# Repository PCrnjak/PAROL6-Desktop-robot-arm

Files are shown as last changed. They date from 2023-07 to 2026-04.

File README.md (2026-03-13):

<div align="center">

# PAROL6-Desktop-robot-arm

</div>

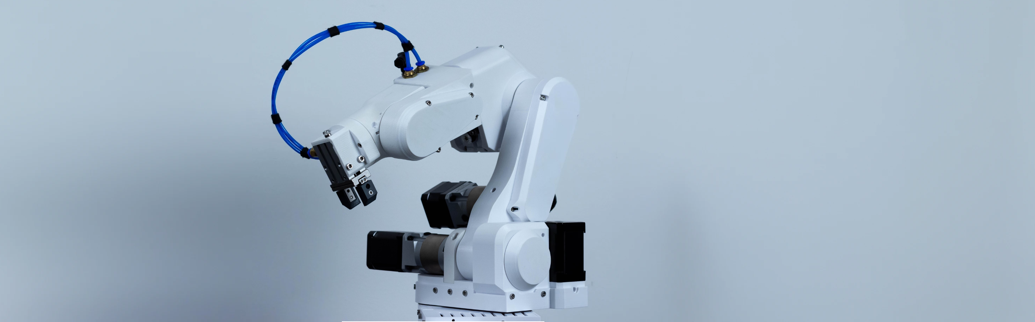
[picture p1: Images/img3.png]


<div align="center">

      Powered by the Robotics Toolbox (https://github.com/petercorke/robotics-toolbox-python) 

<p align="center">
  
  
  
  
  
  
</p>

## [▶️YouTube🔴 Video of Robot in Action!](https://youtu.be/bbrFn3aFLaA)

</div>

## 📖 Project Overview
PAROL6 is a high-performance 3D-printed desktop robotic arm. The design approach of PAROL6 was to be similar to industrial robots in terms of mechanical design, control software, and usability. Control software, GUI, and robots STL files are open-source. 

## How to build / Where to buy?

You can buy the PAROL6 robotic arm on our website: https://source-robotics.com

If you want to Source all the parts yourself and build your own follow these steps:

* Source all the parts from the [BOM](https://github.com/PCrnjak/PAROL6-Desktop-robot-arm/tree/main/BOM)
* Follow [Building instructions](https://github.com/PCrnjak/PAROL6-Desktop-robot-arm/tree/main/Building%20instructions) to assemble your robot
* Follow [DOCS](https://source-robotics.github.io/PAROL-docs/) to get your robot up and running.

## 📚 Resources
- [Official website](https://source-robotics.com)
- [Commander software](https://github.com/PCrnjak/PAROL-commander-software) ------ [Minimal hardware specs!](https://github.com/PCrnjak/PAROL-commander-software/blob/main/confirmed_working_systems.md)
- [Python API](https://github.com/PCrnjak/PAROL6-python-API) ; [Python API legacy](https://github.com/PCrnjak/PAROL6-python-API-Alvar)
- [Building instructions](https://github.com/PCrnjak/PAROL6-Desktop-robot-arm/tree/main/Building%20instructions)
- [BOM](https://github.com/PCrnjak/PAROL6-Desktop-robot-arm/tree/main/BOM)
- [DOCS](https://source-robotics.github.io/PAROL-docs/)
- [Video tutorials](https://youtube.com/playlist?list=PLSueoDrBt5MMTL9O8qAWZiJrNIf8-29Qz&si=Zca3UZKENje9ifow)
- [ROS2 / Moveit simulation](https://github.com/PCrnjak/PAROL6-ROS2-MOVEIT)

### Community projects
- [WEB commander software](https://github.com/Jepson2k/PAROL-Web-Commander)
- [Commander software refactored for easier editing + vision systems](https://github.com/thousands-star/Parol6_Better_Command)
- [PAROL6 Gemini LLM vision control](https://github.com/AlvarEhr/PAROL6-Python-API-Gemini-Vision-Public)
- [PAROL6 Pilot webgui](https://github.com/jointAxis77/pilot)
- [Another GUI](https://github.com/jakubgrzebien1234-creator/PAROL6_GUI)
- [Tic Tac Toe with vision](https://github.com/lennardkiebler-cryptoii/Tic-Tac-Toe-Robot-Project-Parol6/tree/main)
  
## 🌐 More about PAROL6 robotic arm

| YouTube | Instagram | Twitter | LinkedIn |
|---|---|---|---|
|  |  |  |  |

| Discord | Forum | Hackaday | Blog |
|---|---|---| ---|
|  |  |  |  

## ⚠️ Safety, Liability & Disclaimer
This project includes experimental software, hardware designs, and assembly documentation that are still under development and may contain bugs, errors, or incomplete features. By using, building, or modifying this project, you acknowledge that:

* You use this project entirely at your own risk
* You are solely responsible for safe assembly, testing, and operation
* No guarantee is made regarding correctness, safety, or reliability
* The authors are not responsible for any damage, injury, or loss resulting from the use or misuse of this project
* Hardware performance and safety depend on user assembly, component quality, calibration, and handling, which cannot be guaranteed
* This project is provided “as is.” If you choose to build a device yourself using these files, designs, or instructions, you do so without any warranties or guarantees, including regarding safety, reliability, or suitability for any particular purpose.

THIS PROJECT INVOLVES LETHAL VOLTAGES AND OTHER SERIOUS HAZARDS THAT CAN CAUSE SEVERE INJURY. YOU MUST READ THE FULL [SAFETY WARNING AND DISCLAIMER DOCUMENT](SAFETY_WARNING_AND_DISCLAIMER.md)  BEFORE USING ANY PROJECT FILES. BY PROCEEDING, YOU ACKNOWLEDGE AND ACCEPT ALL RISKS AND AGREE TO USE THIS PROJECT ENTIRELY AT YOUR OWN RESPONSIBILITY.

## 💸Support us

The majority of this project is open source and freely available to everyone. Your assistance, whether through donations or advice, is highly valued. Thank you!

 


## 🛡️ Licensing
Project is under GPLv3 Licence

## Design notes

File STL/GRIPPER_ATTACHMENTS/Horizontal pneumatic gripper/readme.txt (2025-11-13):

If anyone interested I made a horizontal mount for the pneumatic griper. 
2x m4 x 10 for the gripper
4x m4 x 10 for the flange 
1x m4 x 6 for mounting it on the shaft
1x m4 x 20mm for the sensor.

First screw the gripper into the mount into the sunk holes
Screw in half way the 6mm screw into the flange
Mount the flange
Screw in the 20mm long one on the side until the end, It should be flush or extruding a bit on the other side
Bottom down the flange on the motor shaft, and tighten the screw.

When the robot is off try to rotate J6 it should move freely.

Prepare the gripper on the actuator, so you are turning J6+ direction until the gripper is flat. That way when you turn off the robot and it homes again, it will home the same, and not 360 rotated around.

The 2 files are the same STLs, but the "custom" was the first one, and i decided to rebuild the robot with self tapping inserts. The flange mounting holes are prepared for those inserts.

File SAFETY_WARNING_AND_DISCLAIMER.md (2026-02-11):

# Safety Warning & Disclaimer
## Definitions

For the purposes of this Safety Warning & Disclaimer, “PROJECT” refers to all materials, files, designs, models, simulations, URDF/MJCF files, control software, firmware, documentation, and any modifications or derivatives provided as part of this robotic arm project.

# Safety Warning

THIS PROJECT INVOLVES ROBOTIC SYSTEMS WITH MOVING MECHANICAL PARTS, ACTUATORS, MOTORS, ELECTRICAL POWER SYSTEMS, AND SOFTWARE-CONTROLLED MOTION. IMPROPER DESIGN, ASSEMBLY, CONFIGURATION, OR OPERATION CAN RESULT IN UNEXPECTED MOVEMENT, PINCH POINTS, CRUSH HAZARDS, COLLISIONS, ELECTRICAL SHOCK, PROPERTY DAMAGE, SERIOUS INJURY, OR DEATH.

Robotic arms can generate significant forces and move at high speeds. Even small systems may cause injury if safety precautions are not followed. Simulation results may not accurately represent real-world behavior, and transferring control software from simulation to physical hardware introduces additional risks.

ONLY QUALIFIED INDIVIDUALS WITH APPROPRIATE TRAINING AND EXPERIENCE IN ROBOTICS, MECHANICAL SYSTEMS, AND ELECTRICAL SYSTEMS SHOULD BUILD, MODIFY, OR OPERATE ANY PHYSICAL IMPLEMENTATION OF THIS PROJECT. ALWAYS FOLLOW APPLICABLE SAFETY STANDARDS, LOCAL REGULATIONS, AND BEST PRACTICES FOR ROBOTIC SYSTEMS. USE APPROPRIATE SAFETY MEASURES INCLUDING, BUT NOT LIMITED TO, EMERGENCY STOPS, PHYSICAL GUARDS, SOFTWARE LIMITS, AND PERSONAL PROTECTIVE EQUIPMENT.

IF YOU DO NOT FULLY UNDERSTAND THE RISKS ASSOCIATED WITH ROBOTIC SYSTEMS, DO NOT USE, BUILD, OR DEPLOY THIS PROJECT ON PHYSICAL HARDWARE.

# Disclaimer

THE PROJECT IS PROVIDED “AS IS”, WITHOUT WARRANTY OF ANY KIND, EXPRESS OR IMPLIED, INCLUDING BUT NOT LIMITED TO THE WARRANTIES OF MERCHANTABILITY, FITNESS FOR A PARTICULAR PURPOSE, OR NON-INFRINGEMENT.

BY USING THIS PROJECT, YOU ACKNOWLEDGE AND ACCEPT ALL RISKS ASSOCIATED WITH ITS USE, INCLUDING RISKS ARISING FROM SOFTWARE ERRORS, SIMULATION INACCURACIES, CONTROL FAILURES, HARDWARE MALFUNCTIONS, OR IMPROPER CONFIGURATION.

IN NO EVENT SHALL THE AUTHORS, CONTRIBUTORS, OR COPYRIGHT HOLDERS BE LIABLE FOR ANY CLAIM, DAMAGE, INJURY, DEATH, OR OTHER LIABILITY, WHETHER IN AN ACTION OF CONTRACT, TORT, OR OTHERWISE, ARISING FROM, OUT OF, OR IN CONNECTION WITH THE PROJECT OR THE USE OR OTHER DEALINGS IN THE PROJECT.

ANY ASSEMBLY, MODIFICATION, DEPLOYMENT, OR OPERATION OF THIS PROJECT — WHETHER IN SIMULATION OR ON PHYSICAL HARDWARE — IS PERFORMED ENTIRELY AT YOUR OWN RISK.

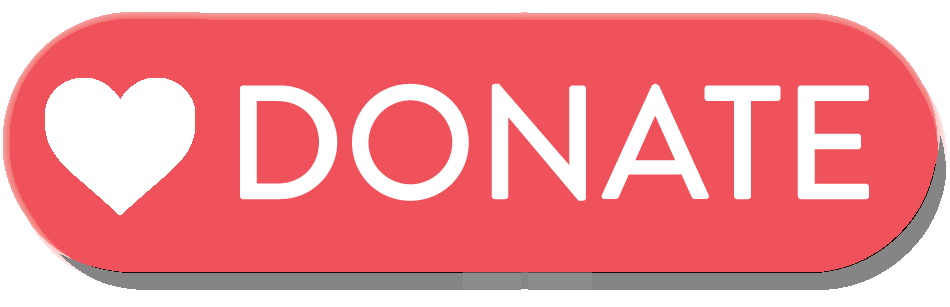
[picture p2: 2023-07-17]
Images/Donate.png

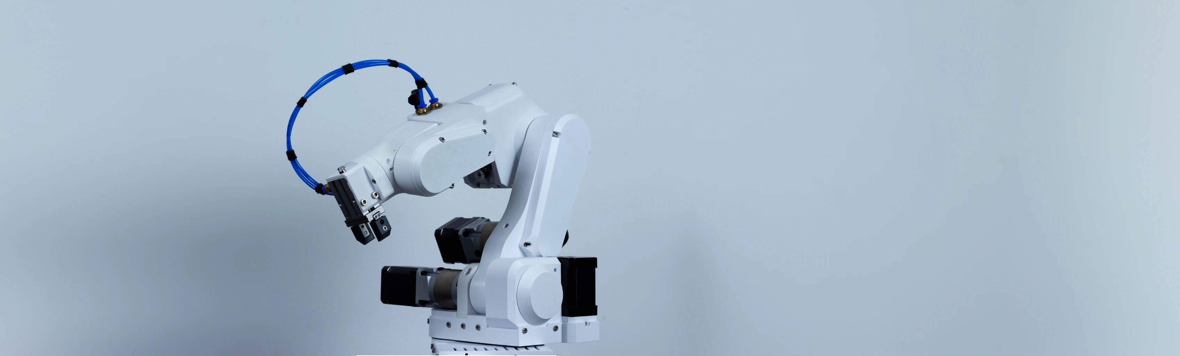
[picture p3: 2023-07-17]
Images/img2 - Copy.png

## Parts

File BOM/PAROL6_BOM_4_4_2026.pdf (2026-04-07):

### This file contains all the parts you need to build PAROL6 robot!

Most items have links where you can buy the item, and some of them are affiliate links. Items like screws, belts and bearings can be bought locally or from many other vendors.

Screws and nuts:
diameter , length | quantity | Description | Link M4x10mm | 20 | DIN 912 / ISO 4762 (hexagon socket head cap) M3x8mm | 10 | 2 mm head height M3x8mm | 50 | DIN 912 / ISO 4762 (hexagon socket head cap) M3x14mm | 30 | DIN 912 / ISO 4762 (hexagon socket head cap) M3 nut | 10 | DIN 912 / ISO 4762 (hexagon socket head cap) M3x25mm | 10 | DIN 912 / ISO 4762 (hexagon socket head cap) M2x10mm | 10 | DIN 912 / ISO 4762 (hexagon socket head cap) M3x16mm | 10 | DIN 912 / ISO 4762 (hexagon socket head cap) M3x6mm | 10 | Pan head phillips M3x12mm | 30 | DIN 912 / ISO 4762 (hexagon socket head cap) M3x35mm | 10 | DIN 912 / ISO 4762 (hexagon socket head cap) M4x16mm | 30 | DIN 912 / ISO 4762 (hexagon socket head cap) M4x14mm | 10 | DIN 912 / ISO 4762 (hexagon socket head cap) M4x50mm | 10 | DIN 912 / ISO 4762 (hexagon socket head cap) M3x15mm | 2 | Tapered screw head Gearboxes: Name in building instructions | Type | quantity | Description | Link
For cheaper gearbox options you can use MG series planetary gearboxes. They have bigger backlash but are cheaper. | Link (https://www.omc-stepperonline.com/mg-series-planetary-gearbox) | Aliexpress Link (https://s.click.aliexpress.com/e/_oBYBoUP) Gearbox 20:1 | Nema 17 20:1 EG precision planetary | 2 | Link | Aliexpress Link Gearbox 10:1 | Nema 17 10:1 EG precision planetary | 1 | Link | Aliexpress Link Motors: Name in building instructions | Type | quantity | Description | Link
Stepper 1 | Nema 17 16Ncm,42x42x20mm | 1 | Link (https://www.omc-stepperonline.com/nema-17-bipolar-1-8deg-16ncm-22-6oz-in-1a-3-7v-42x42x20mm-4-wires-17hs08-1004s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) | Aliexpress Link (https://s.click.aliexpress.com/e/_oo1LTs7)
Stepper 2 | Nema 17 45Ncm,42x42x40mm | 3 | Link (https://www.omc-stepperonline.com/nema-17-bipolar-45ncm-64oz-in-2a-42x42x40mm-4-wires-w-1m-cable-connector-17hs16-2004s1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) | Aliexpress Link (https://s.click.aliexpress.com/e/_oC1Ii0v)
Stepper 3 | Nema 17 65Ncm,42x42x60mm | 2 | Link (https://www.omc-stepperonline.com/nema-17-bipolar-1-8deg-65ncm-92oz-in-2-1a-3-36v-42x42x60mm-4-wires-17hs24-2104s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) | Aliexpress Link (https://s.click.aliexpress.com/e/_opq2ugp) Belts: Name in building instructions | Type | quantity | Description | Link
Joint 1 belt | HTD3 396 | 1 | 6 mm width | Link (https://s.click.aliexpress.com/e/_Dn5FasX)
Joint 3 belt | HTD3 342 | 1 | 6 mm width | Link (https://s.click.aliexpress.com/e/_DeIf41z)
Joint 4 belt | HTD3 201 | 1 | 6 mm width | Link (https://s.click.aliexpress.com/e/_Dc9GUKX)
Joint 5 belt | HTD3 246 | 1 | 6 mm width | Link (https://s.click.aliexpress.com/e/_Dm2tHRd)
| Pulleys: Name in building instructions Type | quantity | Description | Link
J4 pulley, J5 pulley | HTD3M 12 tooth 5mm bore 10mm width | 2 | | Link (https://s.click.aliexpress.com/e/_DFYERWX)
J1 pulley | HTD3M 15 tooth 5mm bore 10mm width | 1 | Link (https://s.click.aliexpress.com/e/_DBVgkVp) Mechanical stuff: Name in building instructions | Type | quantity | Description | Link
Shaft coupler | Shaft coupler | 3 | 8 mm hole shaft, M4 screw holes | Link (https://s.click.aliexpress.com/e/_c2xnQgI7) Bearings: Name in building instructions | Type | quantity | Description | Link
Bearing 1 | AXK3552 | 1 | 35X52X4, needs to have top and bottom plate | Link (https://s.click.aliexpress.com/e/_Dk4bHg7)
Bearing 2 | NSK HR32906J | 5 | Joint 5, 4 and 3 | Link (https://s.click.aliexpress.com/e/_DcJMtBl)
Bearing 3 | NSK HR32907J | 4 | Joint 1 and 2 | Link (https://s.click.aliexpress.com/e/_DcJMtBl)
Tension bearing | Ball bearing 3x8x4 | 20 | Used for belt tension | Link (https://s.click.aliexpress.com/e/_DCjfgFV)
Tension bearing | Ball bearing 3x10x4 | 20 | Used for belt tension | Link (https://s.click.aliexpress.com/e/_DlA33Af)
| Electronics: Name in building instructions Type | quantity | Description | Link
| PAROL control board | 1 | source-robotics.com | Link (https://source-robotics.com/products/parol6-control-board)
| TMC5160 | 6 | Drivers from the links are tested. Use any other at own risk: (https://s.click.aliexpress.com/e/_c3DGg2hx) Link1 | Link2
| Thermal paste | 2 1 | Needed only if your control board has no drivers! 12mm 3-6V | Link (https://s.click.aliexpress.com/e/_oExnMEF) On/Off button Link
| JST PH 2.0mm 200mm 4PIN | 1 1 | For power button | Link (https://s.click.aliexpress.com/e/_DeObQ1D) Noctua NF-A4x20 5V 40mm
| Power connector - male + female | 1 1 | GX16 2PIN M8 sensor Female 4 pin | Link (https://s.click.aliexpress.com/e/_DcHjMfN) Gripper connector (electric) Link
| Power supply | 1 | Any 24V 5A supply (https://s.click.aliexpress.com/e/_olFOM5Z) | Link (https://www.omc-stepperonline.com/edr-120-24-mean-well-120w-24vdc-5a-115-230vac-din-rail-power-supply-edr-120-24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)
| Limit switches | 3 | Type ZW12-3 | Link (https://s.click.aliexpress.com/e/_DBq6eeF)
| Inductive sensor 1 | 1 | 4mm NPN NO - alternative link (https://s.click.aliexpress.com/e/_c3CMbO1h) | Link (https://s.click.aliexpress.com/e/_c40MRkk5)
| Inductive sensor 2 | 1 | GX-F8A | Link (https://s.click.aliexpress.com/e/_c4KR8GBT)
| Inductive sensor 3 | 1 | M5, NPN NO - alternative link (https://s.click.aliexpress.com/e/_c3CMbO1h) | Link (https://s.click.aliexpress.com/e/_c3zGvxrP)
Estop | 1 | Any NC estop | Link (https://s.click.aliexpress.com/e/_DD0VVnd) Cable gland for estop | 1 | PG7 type | Link M3 brass insert | 4 | M3, 6mm lenght | Link
Pneumatic connector - robot | 4 | 4 mm type PM | Link (https://www.aliexpress.com/item/4001338085412.html)
Pneumatic Gripper | 1 | MHZ2-16D | Link (https://s.click.aliexpress.com/e/_DD83OLZ)
Pneumatic gripper connector | 2 | PC4 - M5 | Link (https://s.click.aliexpress.com/e/_DkCJqUL)
Pneumatic tube | 5 meters | 1 meter, 4x2.5mm | Link (https://s.click.aliexpress.com/e/_DEhvFyJ)
xt30 connector female | 1 | used to deliver power to PAROL6 PCB | Link (https://s.click.aliexpress.com/e/_DllR7eL)
Stlink | 1 1 | Use link! Pin order needs to be: SWCLK,SWDIO,GND,3V3,5V Comms to the PC | Link (https://s.click.aliexpress.com/e/_DCPwBnn) USB B cable
5/2 solenoid air valve | 1 | 4mm tube connectors, 5/2, 24V | Link (https://s.click.aliexpress.com/e/_DDrw0Ux)
Vacuum gripper Name in building instructions Type | quantity | Description | Link
Suction cup gripper | 1 | | Link (https://www.aliexpress.com/item/4000538850003.html)
Vacuum generator | 1 | | Link (https://s.click.aliexpress.com/e/_DdTAyOZ)
4mm to 6mm coupler | 1 | | Link (https://s.click.aliexpress.com/e/_DeEEqHR)

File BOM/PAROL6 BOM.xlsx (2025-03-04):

This file contains all the parts you need to build PAROL6 robot!
Most items have links where you can buy the item, and some of them are affiliate links.
Items like screws, belts and bearings can be bought locally or from many other vendors.
 | Screws and nuts:
 | diameter , length | quantity | Description | Link | Alternative links
 | M4x10mm | 20 | DIN 912 / ISO 4762 (hexagon socket head cap)
 | M3x8mm | 10 | 2 mm head height
 | M3x8mm | 50 | DIN 912 / ISO 4762 (hexagon socket head cap)
 | M3x14mm | 30 | DIN 912 / ISO 4762 (hexagon socket head cap)
 | M3 nut | 10 | DIN 912 / ISO 4762 (hexagon socket head cap)
 | M3x25mm | 10 | DIN 912 / ISO 4762 (hexagon socket head cap)
 | M2x10mm | 10 | DIN 912 / ISO 4762 (hexagon socket head cap)
 | M3x16mm | 10 | DIN 912 / ISO 4762 (hexagon socket head cap)
 | M3x6mm | 10 | Pan head phillips
 | M3x12mm | 30 | DIN 912 / ISO 4762 (hexagon socket head cap)
 | M3x35mm | 10 | DIN 912 / ISO 4762 (hexagon socket head cap)
 | M4x16mm | 30 | DIN 912 / ISO 4762 (hexagon socket head cap)
 | M4x14mm | 10 | DIN 912 / ISO 4762 (hexagon socket head cap)
 | M4x50mm | 10 | DIN 912 / ISO 4762 (hexagon socket head cap)
 | M3x15mm | 2 | Tapered screw head
 | Gearboxes:
Name in building instructions | Type | quantity | Description | Link | Alternative (Note these gearboxes have bigger backslash and in turn your robot will be less precise if you use them)
Gearbox 20:1 | Nema 17 20:1 EG precision planetary | 2 | Link (https://www.omc-stepperonline.com/eg-series-planetary-gearbox-gear-ratio-20-1-backlash-20-arc-min-for-nema-17-stepper-motor-eg17-g20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) | Link (https://www.omc-stepperonline.com/eg-series-planetary-gearbox-gear-ratio-20-1-backlash-20-arc-min-for-nema-17-stepper-motor-eg17-g20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) | Link (https://www.omc-stepperonline.com/mg-series-planetary-gearbox-gear-ratio-20-1-backlash-30-arc-min-for-nema-17-stepper-motor-mg17-g20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)
Gearbox 10:1 | Nema 17 10:1 EG precision planetary | 1 | Link (https://www.omc-stepperonline.com/eg-series-planetary-gearbox-gear-ratio-10-1-backlash-15-arc-min-for-nema-17-stepper-motor-eg17-g10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) | Link (https://www.omc-stepperonline.com/eg-series-planetary-gearbox-gear-ratio-10-1-backlash-15-arc-min-for-nema-17-stepper-motor-eg17-g10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) | Link (https://www.omc-stepperonline.com/mg-series-planetary-gearbox-gear-ratio-10-1-backlash-30-arc-min-for-nema-17-stepper-motor-mg17-g10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)
 | Motors:
Name in building instructions | Type | quantity | Description | Link
Stepper 1 | Nema 17 16Ncm,42x42x20mm | 1 | Link (https://www.omc-stepperonline.com/nema-17-bipolar-1-8deg-16ncm-22-6oz-in-1a-3-7v-42x42x20mm-4-wires-17hs08-1004s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) | Link (https://www.omc-stepperonline.com/nema-17-bipolar-1-8deg-16ncm-22-6oz-in-1a-3-7v-42x42x20mm-4-wires-17hs08-1004s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)
Stepper 2 | Nema 17 45Ncm,42x42x40mm | 3 | Link (https://www.omc-stepperonline.com/nema-17-bipolar-45ncm-64oz-in-2a-42x42x40mm-4-wires-w-1m-cable-connector-17hs16-2004s1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) | Link (https://www.omc-stepperonline.com/nema-17-bipolar-45ncm-64oz-in-2a-42x42x40mm-4-wires-w-1m-cable-connector-17hs16-2004s1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)
Stepper 3 | Nema 17 65Ncm,42x42x60mm | 2 | Link (https://www.omc-stepperonline.com/nema-17-bipolar-1-8deg-65ncm-92oz-in-2-1a-3-36v-42x42x60mm-4-wires-17hs24-2104s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) | Link (https://www.omc-stepperonline.com/nema-17-bipolar-1-8deg-65ncm-92oz-in-2-1a-3-36v-42x42x60mm-4-wires-17hs24-2104s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)
 | Belts:
Name in building instructions | Type | quantity | Description | Link
Joint 1 belt | HTD3 396 | 1 | 6 mm width | Link (https://s.click.aliexpress.com/e/_Dn5FasX)
Joint 3 belt | HTD3 342 | 1 | 6 mm width | Link (https://s.click.aliexpress.com/e/_DeIf41z)
Joint 4 belt | HTD3 201 | 1 | 6 mm width | Link (https://s.click.aliexpress.com/e/_opwpKMM)
Joint 5 belt | HTD3 246 | 1 | 6 mm width | Link (https://s.click.aliexpress.com/e/_ompnL9w)
 | Pulleys:
Name in building instructions | Type | quantity | Description | Link
J4 pulley, J5 pulley | HTD3M 12 tooth 5mm bore 10mm width | 2 |  | Link (https://s.click.aliexpress.com/e/_DFYERWX)
J1 pulley | HTD3M 15 tooth 5mm bore 10mm width | 1 |  | Link (https://s.click.aliexpress.com/e/_DBVgkVp)
 | Mechanical stuff:
Name in building instructions | Type | quantity | Description | Link
Shaft coupler | Shaft coupler | 3 | 8 mm hole shaft, M4 screw holes | Link (https://s.click.aliexpress.com/e/_DdSVv79)
 | Bearings:
Name in building instructions | Type | quantity | Description | Link
Bearing 1 | AXK3552 | 1 | 35X52X4, needs to have top and bottom plate | Link (https://s.click.aliexpress.com/e/_Dk4bHg7)
Bearing 2 | NSK HR32906J | 5 | Joint 5, 4 and 3 | Link (https://s.click.aliexpress.com/e/_oEMEtzK)
Bearing 3 | NSK HR32907J | 4 | Joint 1 and 2 | Link (https://s.click.aliexpress.com/e/_DcJMtBl)
Tension bearing | Ball bearing 3x8x4 | 20 | Used for belt tension | Link (https://s.click.aliexpress.com/e/_DCjfgFV)
Tension bearing | Ball bearing 3x10x4 | 20 | Used for belt tension | Link (https://s.click.aliexpress.com/e/_DlA33Af)
 | Electronics:
Name in building instructions | Type | quantity | Description | Link
 | PAROL control board | 1 | source-robotics.com | Link (https://source-robotics.com/products/parol6-control-board)
 | TMC5160 | 6 | Drivers from the links are tested. Use any other at own risk: Link1 (https://s.click.aliexpress.com/e/_opQvIZd) | Link2 (https://s.click.aliexpress.com/e/_Dd8Cjkb)
 | Thermal CEMENT | 2 | Needed only if your control board has no drivers! | Link (https://s.click.aliexpress.com/e/_opNwYbw)
 | On/Off button | 1 | 12mm 3-6V | Link (https://s.click.aliexpress.com/e/_DBpZV3h)
 | JST PH 2.0mm 200mm 4PIN | 1 | For power button | Link (https://s.click.aliexpress.com/e/_DeObQ1D)
 | Noctua NF-A4x20 5V 40mm | 1
 | Power connector - male + female | 1 | GX16 2PIN | Link (https://s.click.aliexpress.com/e/_DcHjMfN)
 | Gripper connector (electric) | 1 | M8 sensor Female 4 pin | Link (https://s.click.aliexpress.com/e/_DDQz9iP)
 | Power supply | 1 | Any 24V 5A supply | Link (https://www.omc-stepperonline.com/edr-120-24-mean-well-120w-24vdc-5a-115-230vac-din-rail-power-supply-edr-120-24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)
 | Limit switches | 3 | Type ZW12-3 | Link (https://s.click.aliexpress.com/e/_DBq6eeF)
 | Inductive sensor 1 | 1 | 4mm NPN NO | Link (https://s.click.aliexpress.com/e/_Dk60HT9)
 | Inductive sensor 2 | 1 | GX-F8A | Link (https://s.click.aliexpress.com/e/_DEOqTIT)
 | Inductive sensor 3 | 1 | M5, NPN NO | Link (https://s.click.aliexpress.com/e/_DDhHytl)
 | Estop 19mm | 1 | Any NC estop | Link (https://s.click.aliexpress.com/e/_okbRavW)
 | Cable gland for estop | 1 | PG7 type | Link (https://s.click.aliexpress.com/e/_DdJj62p)
 | M3 brass insert | 4 | M3, 6mm lenght | Link (https://s.click.aliexpress.com/e/_DmZR9AN)
 | Pneumatic connector - robot | 4 | 4 mm type PM | Link (https://www.aliexpress.com/item/4001338085412.html)
 | Pneumatic Gripper | 1 | MHZ2-16D | Link (https://s.click.aliexpress.com/e/_DD83OLZ)
 | Pneumatic gripper connector | 2 | PC4 - M5 | Link (https://s.click.aliexpress.com/e/_DkCJqUL)
 | Pneumatic tube | 5 meters | 1 meter, 4x2.5mm | Link (https://s.click.aliexpress.com/e/_DEhvFyJ)
 | xt30 connector female | 1 | used to deliver power to PAROL6 PCB | Link (https://s.click.aliexpress.com/e/_DllR7eL)
 | Stlink | 1 | Use link! Pin order needs to be: SWCLK,SWDIO,GND,3V3,5V | Link (https://s.click.aliexpress.com/e/_DCPwBnn)
 | USB B cable | 1 | Comms to the PC
 | 5/2 solenoid air valve | 1 | 4mm tube connectors, 5/2, 24V | Link (https://s.click.aliexpress.com/e/_DDrw0Ux)
 | Vacuum gripper
Name in building instructions | Type | quantity | Description | Link
 | Suction cup gripper | 1 |  | Link (https://www.aliexpress.com/item/4000538850003.html)
 | Vacuum generator | 1 |  | Link (https://s.click.aliexpress.com/e/_DdTAyOZ)
 | 4mm to 6mm coupler | 1 |  | Link (https://s.click.aliexpress.com/e/_DeEEqHR)

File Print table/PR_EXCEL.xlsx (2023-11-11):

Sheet: 3D printed parts stats
THIS TABLE HAS SUGGESTIONS ON WHAT SETTINGS TO USE!
IT IS NOT CRITICAL TO FOLLOW IT BUT NOTE THAT THESE SETTINGS HAVE BEEN TESTED ON MUTLIPLE ROBOTS!
Part name | Position in arm | Supports | mass (g) | Infill type | Infill % | Time | Cooling % | Layer h | Top layers | Bot layers | Perimeters
Wrist | J6 | Minimal | 77.65 | honey | 40 | 7h51m | 15 | 0.2 LA | 6 | 4 | 3
Pneumatic gripper holder | J6 | None | 31 | honey | 40 | 2h52m | 15 | 0.2 LA | 6 | 4 | 3
J5 pulley | J5 | None | 20 | honey | 40 | 2h | 15 | 0.2 LA | 6 | 4 | 3
J5 part | J5 | Minimal | 114 | honey | 30 | 10h | 15 | 0.2 LA | 6 | 4 | 3
J5 belt lid | J5 | None | 20 | honey | 15 |  | 15 | 0.2 LA | 6 | 4 | 3
J5 electronics lid | J5 | None | 20 | honey | 15 |  | 15 | 0.2 LA | 6 | 4 | 3
Elbow part | J4 | alot | 215 | honey | 25 | 16h | 15 | 0.2 LA | 6 | 4 | 3
J4 limiter | J4 | None | 1 | honey | 80 | 2m | 15 | 0.2 LA | 6 | 4 | 3
J4 bearing backplate | J4 | None |  | honey |  |  | 15 | 0.2 LA | 6 | 4 | 3
 | J4 | None |  | honey |  |  | 15 | 0.2 LA | 6 | 4 | 3
Elbow lid 1 | J4 | None | 20 | honey | 20 | 1h46m | 15 | 0.2 LA | 6 | 4 | 3
Elbow lid 2 | J4 | None | 4 | honey | 20 | 15m | 15 | 0.2 LA | 6 | 4 | 3
Upper arm | J3 | Minimal | 220 | honey | 35 | 18h | 15 | 0.2 LA | 6 | 4 | 3
J3 limit switch lid | J3 | None | 4 | honey | 50 | 21m | 15 | 0.2 LA | 6 | 4 | 3
J3 pulley | J3 | None | 25 | honey | 50 | 2h42m | 15 | 0.2 LA | 6 | 4 | 3
J3 pulley input | J3 | None | 14 | honey | 50 | 1h16m | 15 | 0.2 LA | 6 | 4 | 3
Upper arm cover | J3 | minimal | 34 | honey | 15 | 2h | 15 | 0.2 LA | 6 | 4 | 3
J2_cover | J2 | None | 10 | honey | 20 | 42m | 15 | 0.2 LA | 6 | 4 | 3
J2_bering backplate | J2 | None | 10 | honey | 20 | 42m | 15 | 0.2 LA | 6 | 4 | 3
J1_belt_cover | J2 | None | 37 | honey | 20 | 2h | 15 | 0.2 LA | 6 | 4 | 3
J2_stepper_blocker | J2 | None | 7 | honey | 20 | 15m | 15 | 0.2 LA | 6 | 4 | 3
J1_turret_motor_holder | J2 | Minimal | 53 | honey | 80 | 6h | 15 | 0.2 LA | 6 | 4 | 3
J1_turret | J1 | Minimal | 210 | honey | 25 | 18h | 15 | 0.2 LA | 6 | 4 | 3
J1_lid_motor | J1 | Minimal | 9 | honey | 25 | 51m | 15 | 0.2 LA | 6 | 4 | 3
J1_rotation_shaft | J1 | none | 31 | honey | 50 | 3h34m | 15 | 0.2 LA | 6 | 4 | 3
J2_shaft | J2 | none | 43 | honey | 50 | 4h41m | 15 | 0.2 LA | 6 | 4 | 3
Electronics_cover | J1 | Minimal | 80 | honey | 20 | 6h | 15 | 0.2 LA | 6 | 4 | 3
J2 limit switch cover | J2 | Minimal | 3 | honey | 25 | 13m | 15 | 0.2 LA | 6 | 4 | 3
Electronics_case | J1 | Minimal |  | honey | 50 |  | 15 | 0.2 LA | 6 | 4 | 3
Fan_cover | J1 | Minimal |  | honey | 20 |  | 15 | 0.2 LA | 6 | 4 | 3
J1_bottom_lid | J1 | Minimal |  | honey | 25 |  | 15 | 0.2 LA | 6 | 4 | 3
Main_base | J1 | Minimal |  | honey | 50 |  | 15 | 0.2 LA | 6 | 4 | 3
HTD_48_J5_PULLEY | J5 | Minimal |  | honey | 60 |  | 15 | 0.2 LA | 6 | 4 | 3
J4_output_pulley | J1 | Minimal |  | honey | 50 |  | 15 | 0.2 LA | 6 | 4 | 3
Pneumatic_gripper_holder | Gripper | Minimal |  | honey | 30 |  | 15 | 0.2 LA | 6 | 4 | 3
J1_backplate | J1 | Minimal |  | honey | 50 |  | 15 | 0.2 LA | 6 | 4 | 3
J1_turret | J1 | Minimal |  | honey | 45 |  | 15 | 0.2 LA | 6 | 4 | 3
J2_limit_switch_cover |  | Minimal |  | honey | 50 |  | 15 | 0.2 LA | 6 | 4 | 3
J1_stepper_block | J1 | Minimal |  | honey | 45 |  | 15 | 0.2 LA | 6 | 4 | 3
Upper_arm_wires_cover | J3 | Minimal |  | honey | 45 |  | 15 | 0.2 LA | 6 | 4 | 3
38_pulley_J3 | J3 | Minimal |  | honey | 70 |  | 15 | 0.2 LA | 6 | 4 | 3
42_pulley | J3 | Minimal |  | honey | 70 |  | 15 | 0.2 LA | 6 | 4 | 3

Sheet: Wire_markings
4pin | Joint
 | 5
 | 4
 | 6
 | 2
 | 3
No color | 1
3pin | Joint
 | 4
 | 6
2pin | Joint

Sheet: BOM for prototype
Screws and nuts: |  |  | Gearboxes: |  | Bearings:
diameter , length | Type | quantity | Type | quantity | Type | quantity
 |  |  | Motors:
 |  |  | Type | quantity
 |  |  |  |  | Mechanical stuff
 |  |  | Belts |  | type | quantity
 |  |  | Type | quantity
 |  |  | Pulleys:
 |  |  | Type | quantity | Electronics
 |  |  |  |  | type | quantity

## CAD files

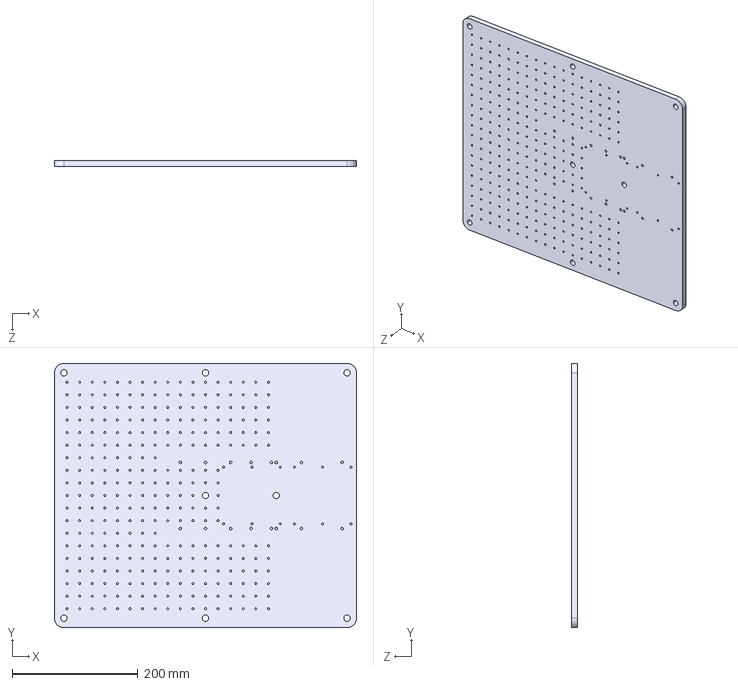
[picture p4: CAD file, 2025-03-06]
mounting plates/big_base.STEP
480.0 x 420.0 x 10.0 mm

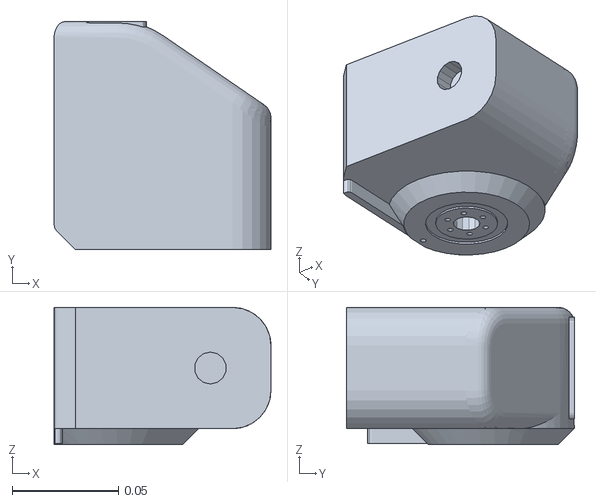
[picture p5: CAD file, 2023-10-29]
PAROL6_URDF/PAROL6/meshes/L3.STL
0.102 x 0.107 x 0.0645

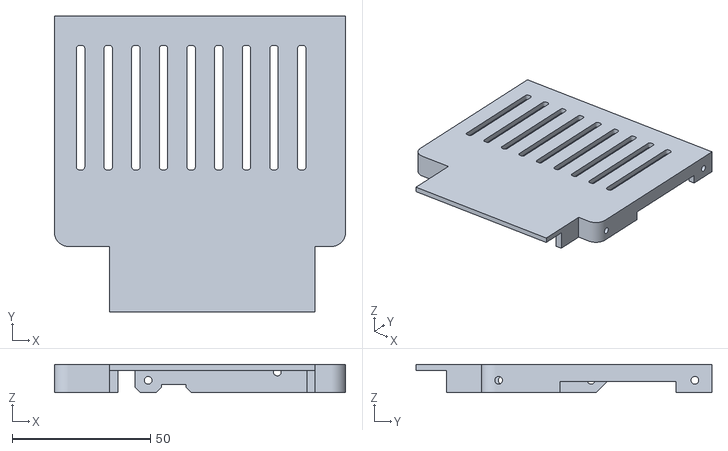
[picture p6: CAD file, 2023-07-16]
STL/BASE/lid_electronics.STL
105.4 x 107.1 x 10.3

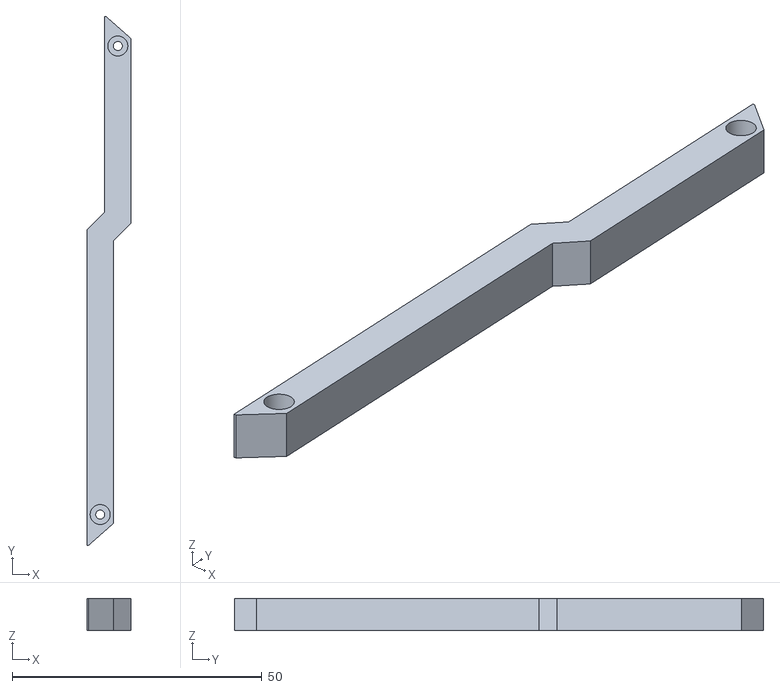
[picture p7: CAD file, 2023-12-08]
STL/ELBOW/J1_wires_cover_rework.STL
8.83 x 105.8 x 6.50

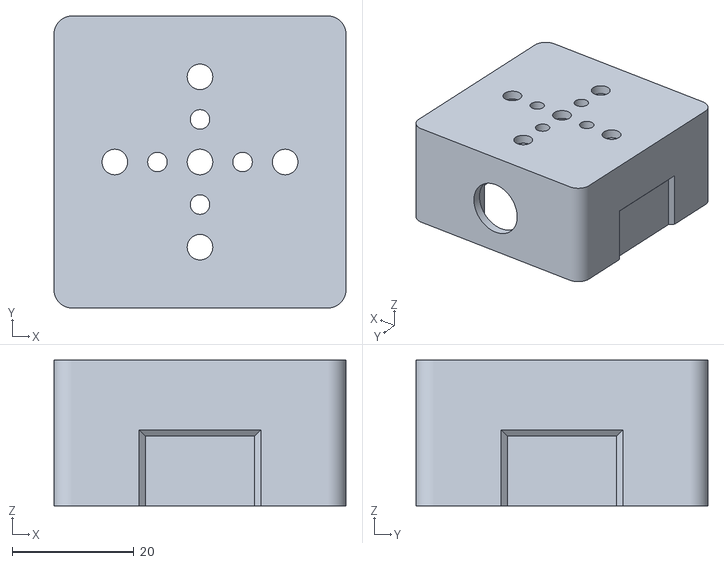
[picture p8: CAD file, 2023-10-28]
STL/ESTOP/ESTOP_BOTTOM.STL
48.0 x 48.0 x 24.0

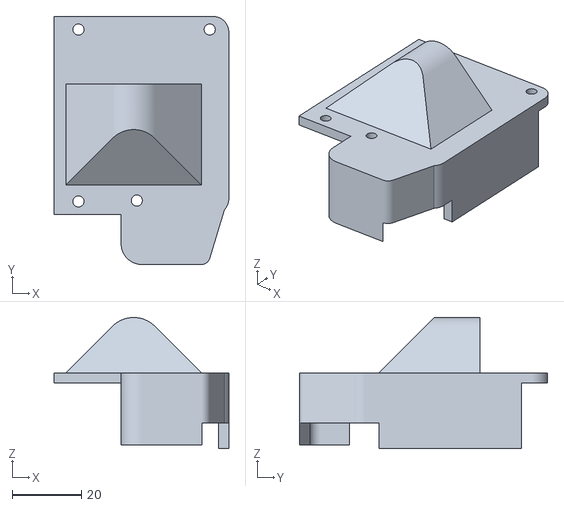
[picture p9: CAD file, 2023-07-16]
STL/FOREARM/J5_electronics_lid.STL
50.3 x 71.4 x 37.7

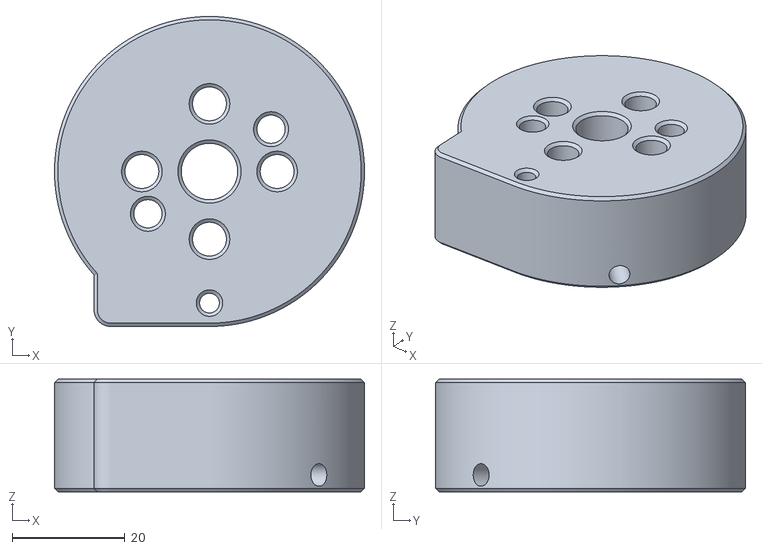
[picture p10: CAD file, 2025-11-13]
STL/GRIPPER_ATTACHMENTS/Horizontal pneumatic gripper/Pneumatic_gripper_holder_custom.stl
55.0 x 55.0 x 20.0

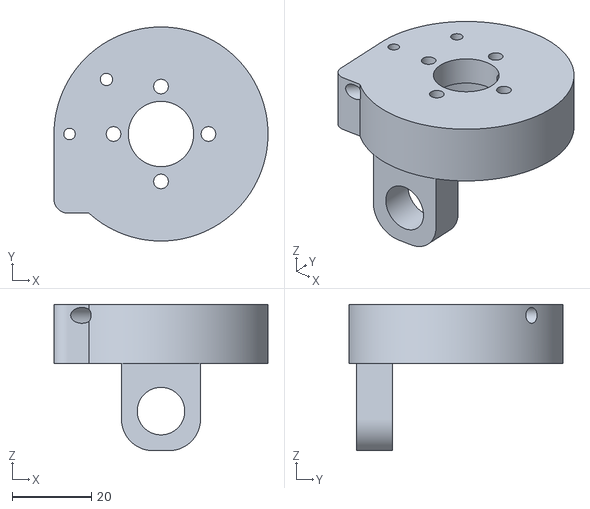
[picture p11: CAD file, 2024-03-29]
STL/GRIPPER_ATTACHMENTS/vacuum_gripper_holder.STL
54.1 x 54.1 x 37.0

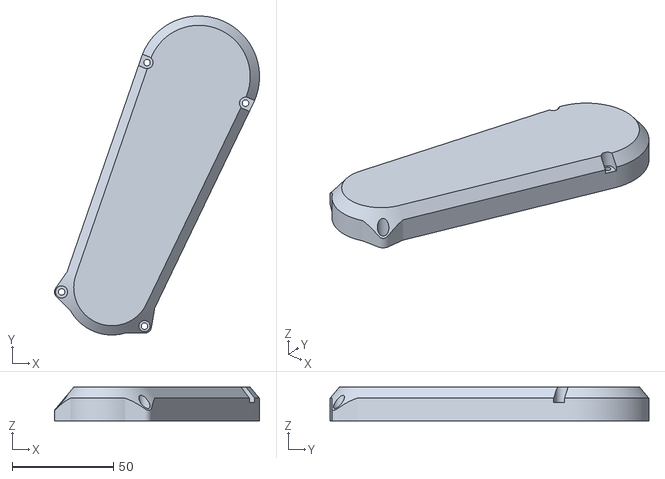
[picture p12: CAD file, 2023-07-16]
STL/UPPER_ARM/Upper_arm_cover.STL
101.4 x 157.7 x 16.7

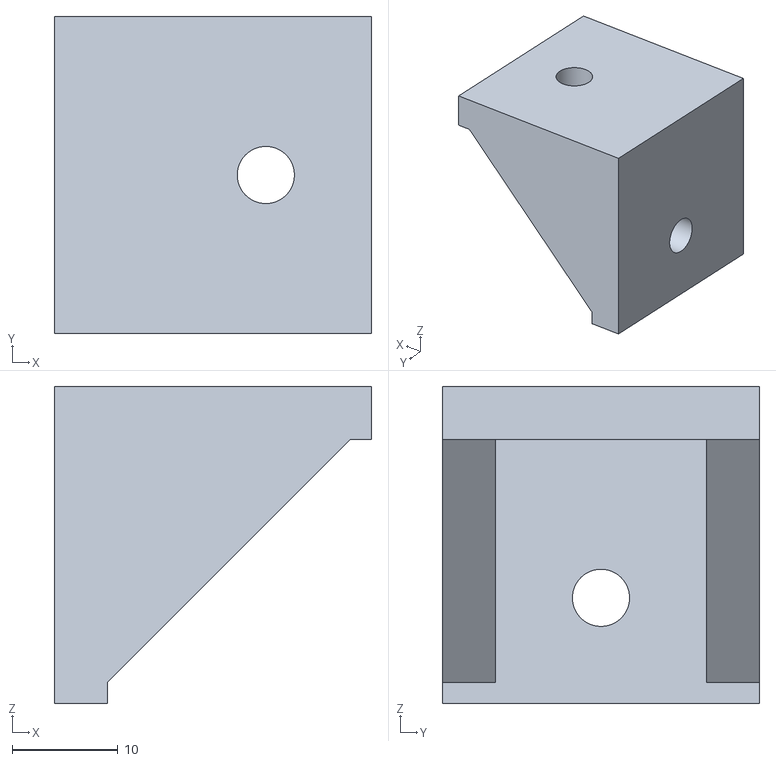
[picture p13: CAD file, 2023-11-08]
STL/UTILITY/connectors_4_alu_profiles.STL
30.0 x 30.0 x 30.0

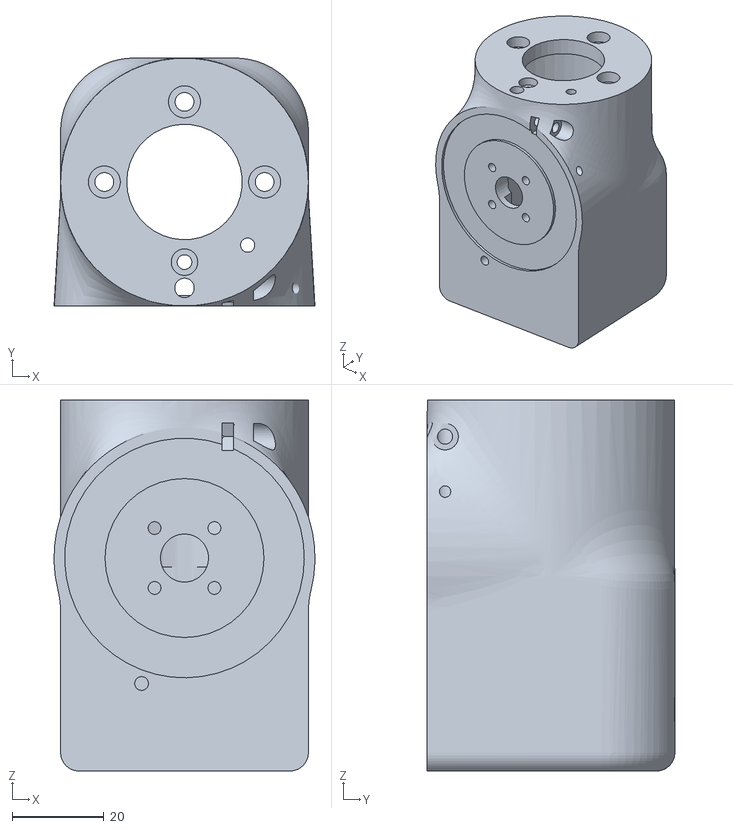
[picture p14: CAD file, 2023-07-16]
STL/WRIST/wrist.STL
57.0 x 54.1 x 81.0

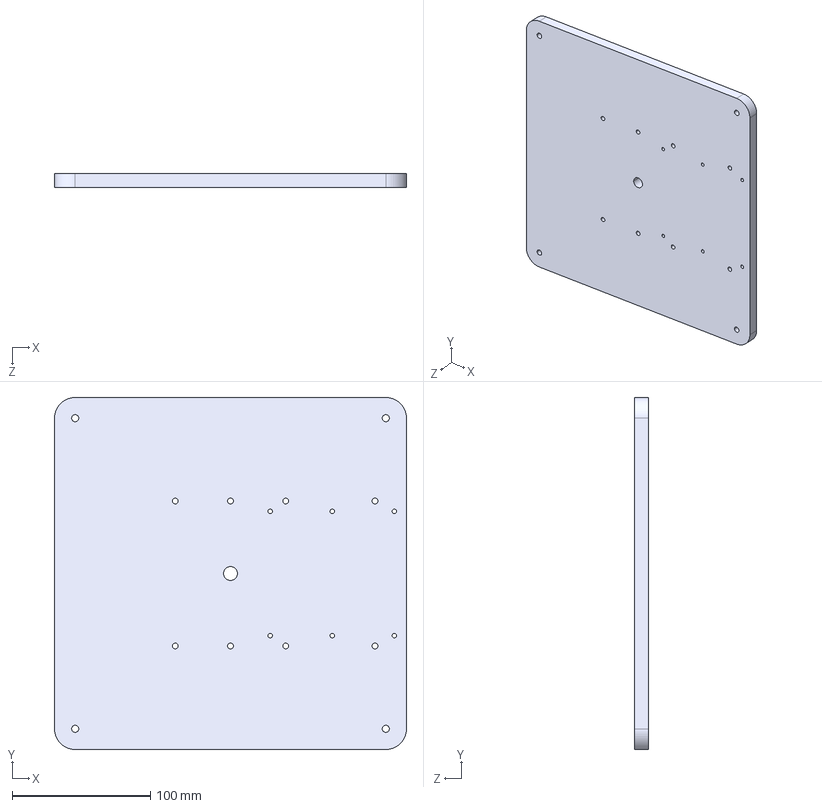
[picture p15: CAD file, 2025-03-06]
mounting plates/small_base.STEP
255.0 x 255.0 x 10.0 mm

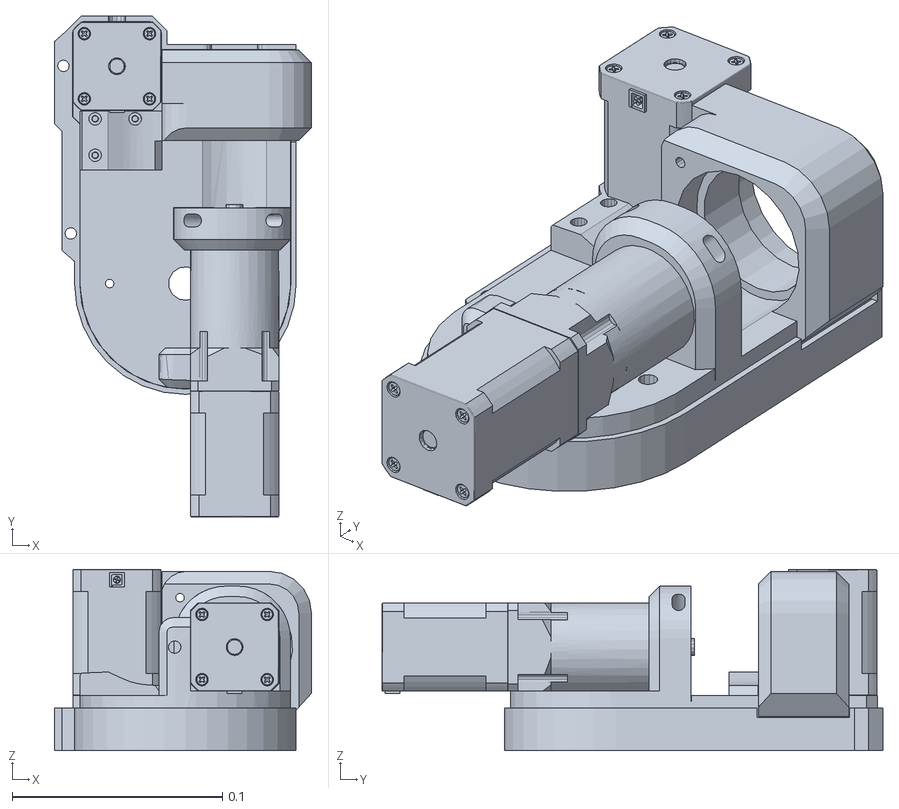
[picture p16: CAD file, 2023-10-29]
PAROL6_URDF/PAROL6/meshes/L1.STL
0.122 x 0.238 x 0.0863

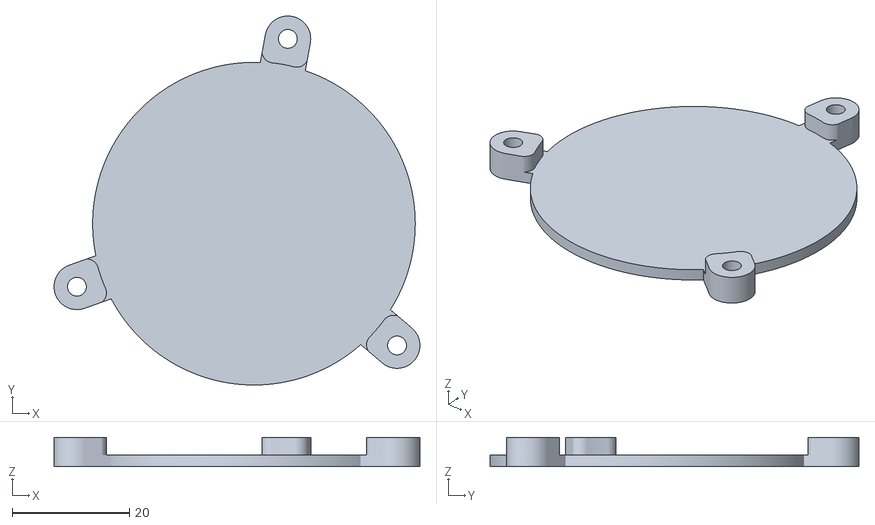
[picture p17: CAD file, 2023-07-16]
STL/BASE/J1_bottom_lid.STL
62.3 x 62.8 x 5.00

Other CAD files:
STL/ELBOW/J4_limiter.STL
STL/ESTOP/ESTOP_TOP.STL
STL/GRIPPER_ATTACHMENTS/Horizontal pneumatic gripper/Pneumatic_gripper_holder_horizontal.stl
PAROL6_URDF/PAROL6/meshes/L2.STL
PAROL6_URDF/PAROL6/meshes/L4.STL
PAROL6_URDF/PAROL6/meshes/L5.STL
PAROL6_URDF/PAROL6/meshes/L6.STL
PAROL6_URDF/PAROL6/meshes/base_link.STL
STL/ELBOW/Elbow_lid_2.STL
STL/ELBOW/J4_bearing_backplate.STL
STL/GRIPPER_ATTACHMENTS/Gripper_ARMS.STL
STL/GRIPPER_ATTACHMENTS/Pneumatic_gripper_holder.STL
STL/SHOULDER/J1_backplate.STL
STL/SHOULDER/J1_belt_cover_rework.STL
STL/SHOULDER/J1_rotation_shaft.STL
STL/SHOULDER/J1_turret_motor_holder.STL
STL/SHOULDER/J2_limit_switch_cover.STL
STL/SHOULDER/J2_stopper_block.STL
STL/UPPER_ARM/J2_bearing_backplate.STL
STL/UPPER_ARM/J2_shaft.STL
STL/UPPER_ARM/J3_limit_switch_cover.STL
STL/UPPER_ARM/Upper_arm_wires_cover.STL

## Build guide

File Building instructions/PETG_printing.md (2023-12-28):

PETG stands out among 3D printing materials for its versatility, offering a blend of strength and ease of use. Its popularity has surged as a viable alternative to PLA due to its distinctive properties. PETG, short for Polyethylene Terephthalate Glycol-modified, undergoes a structural change enhancing transparency, durability, and printability.

When considering PETG, it's essential to weigh its attributes against other materials like PLA and ABS:

* Rigidity: PETG and ABS exhibit similar rigidity, while PLA tends to be slightly more rigid.
* Strength: PETG generally outperforms PLA and boasts superior layer adhesion compared to ABS.
* Heat Resistance: PETG softens at around 80ºC, offering moderate heat resistance, whereas ABS leads with a softening point of 105ºC. PLA softens at a lower temperature of 50ºC.
* Odourless Printing: Unlike ABS, PETG doesn't emit odours during printing.
* Recyclability: PETG's widespread usage has led to widespread recycling infrastructure.

To successfully print with PETG:

* Hotend Temperature: Set the hotend temperature between 220-250ºC, compatible with various 3D printers, including those with all-metal hotends or inner PTFE tubes.
* Bed Temperature: Utilize a heated bed at 60-90ºC and consider using adhesive, such as paper glue, for better print adhesion.
* Printer Enclosure: Although not mandatory, maintaining stable room temperatures is advisable to ensure consistent print quality.
* Layer Fan: Employ a layer fan while printing PETG.
* Warping: PETG's limited thermal contraction reduces warping, resulting in parts with accurate dimensions.
* 
By understanding these characteristics and adhering to optimal printing conditions, PETG can produce robust prints with high dimensional accuracy, catering to a variety of applications.

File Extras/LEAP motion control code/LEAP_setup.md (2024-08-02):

## Setup leap motion

* install python 3.8
* install https://github.com/ano0002/Leap-Motion-Python-3.8
* install this sdk: https://leap2.ultraleap.com/gemini-downloads/ legacy downloads 3.2

## Setup parol6

* Run the PAROL6_LEAP_comms_LEAP.py
* press h to home the robot
* after that press j to go to start position
* NOTE you can always stop the robot with the estop. if stopped that way you need to release the estop and press e on keyboard

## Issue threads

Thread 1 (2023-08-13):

Outdated links to previous project

fraseyboo, 2023-08-13:
It looks like the BOM and build instructions links in your README to your Faze4 robotic arm page rather than the respective ones for this project. Should be an easy fix.

PCrnjak, 2023-08-15:
Fixed thank you!

Closed 2023-08-17.

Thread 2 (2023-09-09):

Minor doc change: incorrect email, no links except for insta, minor corrections

mkinney, 2023-09-09:
Really impressive project. Docs remind me of Lego instructions. (which is a huge compliment)

1) Looks like the email is probably incorrect on page 3 of "Building instructions.pdf".

"● Or send us an email at: sourcerobots@gmai.com" (missing the "l" in gmail?)

2) Only the Instagram link is present (page 3). Did you want to add links to the other social media locations?

3) Page 4 "Some parts are not show" should probably be "Some parts are not shown"

4) Page 8, two "esthetic" should be "aesthetic"

5) On page 8, "If you are not using it you risk destroying your plastic parts" should probably be changed to something like, "If not torqued, then you risk destroying the plastic parts." (if that's what you were trying to state)

6) On page 8, "Attaching shaft couplers to motor shafts demands blue threadlocker." "demands" should probably be changed to "requires".

7) Imbus might be called an Allen or hex key wrench in the US

The rest looks like it is still a work in progress.

I'm assuming there will be more info on the board. (where to purchase, how to assemble, how to test with each of the steppers before assembly, etc.)

Hope this helps.

minor edit to this issue: If you supply the source docs for the pdf, PRs could be made directly.

PCrnjak, 2023-09-09:
Wow, thank you! I didn't have enough time to grammar check and edit everything when I was writing that but over time I will fix them all.  About PCB there is a signup link here: https://forms.gle/XkSvStwnQxw1f8xL8
I will keep this open so I don't forget what needs to be done! Thank you!

movefasta, 2023-09-11:
@PCrnjak  Also hackaday link forward to Faze4 page. Actually it should be https://hackaday.io/project/191860-parol6-desktop-robotic-arm

PCrnjak, 2023-09-11:
Fixed that thank you!

PCrnjak, 2023-10-29:
Fixed all thank you!

Closed 2023-10-29.

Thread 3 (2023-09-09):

BOM link in README is incorrect

corndog2000, 2023-09-09:
The link for BOM goes to an error 404 page.

PCrnjak, 2023-09-09:
Updated BOM thank you!

PCrnjak, 2023-09-09:
Closed

Closed 2023-09-09.

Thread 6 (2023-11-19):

Printing material

743814ck3y3, 2023-11-19:
The printing material is missing.

PCrnjak, 2023-11-19:
If you are talking about material that needs to be used to print the arm it is in the building instructions and docs. It is recommended to use PETG

Closed 2023-11-21.

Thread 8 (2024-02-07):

Where is the PCB

burak1000, 2024-02-07:
I think this is a type of open source project ok great

1-  I want buy a PAROL6 arm but it is sold out.
2- Ok  so I will print STL files and i will buy a control board ...   tadaaa control board sold out.
3 - No problem I can order a PCB and build myself this board  Supriseee There is no PCB files

Why do you relase this project please help me understand

 Also there is no original Drawing files (Fusion or Solid). If you dont want anyone to do this arm, please dont share STL files too. there is no difference between them.  because when we start this project and our days will gone and when a problem appear no way to fix it without original 3D files. I dont believe this STL files is perfect

If you want share an open sourced project please share it
Thanks

PCrnjak, 2024-02-07:
Hey!
We are currently out of stock and will have next batch of PCBs available by the end of this month. About original files they are available in STEP format on our website for purchase. As it is stated on GitHub "Control software, GUI, and robots STL files are open-source."    If you have any more questions send us an email at info@source-robotics.com

tcurdt, 2024-08-16:
@PCrnjak I think the point was that the PCBs are apparently not open source?

burak1000, 2024-08-16:
> @PCrnjak I think the point was that the PCBs are apparently not open source?

you are absolutely right

Closed 2024-02-08.

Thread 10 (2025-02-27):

Not sure if I'm missing or it's not there - PCB Schematics

SangramChavan, 2025-02-27:
Is it complete opensource ? PCB Schematics ?

PCrnjak, 2025-03-08:
PCBs are not open source

Closed 2025-03-08.

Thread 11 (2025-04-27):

Printing profile

Samir-driod, 2025-04-27:
Hi,

I was wondering if it’s possible to get a Bambulab printing file from you. If not, could you provide the settings for printing the parts? I think the Excel file is a bit out of date and missing one infile % value.

PCrnjak, 2025-05-23:
The table is not out of date, just follow infills and top/bottom layer recommendations and you are good

imrahil, 2025-09-25:
it is outdated, it is.... I don’t know what 3D printer you’re using, but my Bambu Lab X1C shows that printing each part takes half the time listed in the Excel sheet. 3mf files with correct positioning would be awesome. I can help if you want :)

Closed 2025-05-23.

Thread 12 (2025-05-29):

STLs Violate GPL v3

jonathankoren, 2025-05-29:
According to https://source-robotics.com/products/parol6-step-files

```STEP files for PAROL6 robotic arm!
This format of files can be used to edit and make modifications to the robot for your own needs! Files do not include the assembly of the whole robot, only individual STEP files of every part of the robot.

PAROL6 software and STL files are licensed as a GPL3 project and are open source.
STEP files of the PAROL6 robot are not open source and as such should not be shared without permission. For more information contact us at info@source-robotics.com```

This doesn't make any sense. This is a textbook GPL violation. https://www.gnu.org/licenses/gpl-3.0.en.html defines "source code" as, `the preferred form of the work for making modifications to it. “Object code” means any non-source form of a work.`

Under the GPL's definition, the STEP files (which you describe as being necessary for making modifications) would be "source code", and thus needs to be distributed with the STLs, which would be analogous to the compiled form for end use.

You have to make the STEP files available. That's what the GPL requires.

I understand what you're trying to do, but this isn't the way.

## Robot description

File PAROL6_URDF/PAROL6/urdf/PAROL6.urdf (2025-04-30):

<?xml version="1.0" encoding="utf-8"?>
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
<robot name="parol6">

  <link name="world"/>
  <joint name="base_joint" type="fixed">
    <parent link="world"/>
    <child link="base_link"/>
    <origin rpy="0 0 0" xyz="0.0 0.0 0.00"/>
  </joint>


  <link name="base_link">
    <inertial>
      <origin xyz="-0.0274562034602567 -0.00137265400595656 0.031237920982338" rpy="0 0 0" />
      <mass value="0.812661291810144" />
      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
    </inertial>
    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
  </link>
  <link name="L1">
    <inertial>
      <origin xyz="0.00524529891406311 0.0289722820784871 0.0992791429452917" rpy="0 0 0" />
      <mass value="0.644800830530233" />
      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
    </inertial>
    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
  </link>
  <joint name="L1" type="revolute">
    <origin xyz="0 0 0" rpy="0 0 0" />
    <parent link="base_link" />
    <child link="L1" />
    <axis xyz="0 0 1" />
    <limit lower="-1.7" upper="1.7" effort="300" velocity="3" />
  </joint>
  <link name="L2">
    <inertial>
      <origin xyz="-0.0094181617193695 -0.0783879603613605 0.0369429741417731" rpy="0 0 0" />
      <mass value="0.512334779399788" />
      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
    </inertial>
    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
  </link>
  <joint name="L2" type="revolute">
    <origin xyz="0.0234207210610375 0 0.1105" rpy="-1.5707963267949 0 0" />
    <parent link="L1" />
    <child link="L2" />
    <axis xyz="0 0 1" />
    <limit lower="-0.98" upper="1" effort="300" velocity="3" />
  </joint>
  <link name="L3">
    <inertial>
      <origin xyz="0.0155509885239593 -0.0191127686426613 -0.00153322577917236" rpy="0 0 0" />
      <mass value="0.550970997806044" />
      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
    </inertial>
    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
  </link>
  <joint name="L3" type="revolute">
    <origin xyz="0 -0.18 0" rpy="3.1416 0 -1.5708" />
    <parent link="L2" />
    <child link="L3" />
    <axis xyz="0 0 -1" />
    <limit lower="-2" upper="1.3" effort="300" velocity="3" />
  </joint>
  <link name="L4">
    <inertial>
      <origin xyz="0.000947028430634433 -0.008978947112462 -0.0924798659827059" rpy="0 0 0" />
      <mass value="0.39346362633915" />
      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
    </inertial>
    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
  </link>
  <joint name="L4" type="revolute">
    <origin xyz="0.0435 0 0" rpy="1.5707963267949 0 3.14159265358979" />
    <parent link="L3" />
    <child link="L4" />
    <axis xyz="0 0 -1" />
    <limit lower="-2" upper="2" effort="300" velocity="3" />
  </joint>
  <link name="L5">
    <inertial>
      <origin xyz="6.7162171684676E-06 -0.00621420980825221 -0.000960871025916146" rpy="0 0 0" />
      <mass value="0.185171777001718" />
      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
    </inertial>
    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
  </link>
  <joint name="L5" type="revolute">
    <origin xyz="0 0 -0.17635" rpy="-1.5708 0 0" />
    <parent link="L4" />
    <child link="L5" />
    <axis xyz="0 0 -1" />
    <limit lower="-2.1" upper="2.1" effort="300" velocity="3" />
  </joint>
  <link name="L6">
    <inertial>
      <origin xyz="0.00632955087228015 -0.000453856352095022 -0.0554441567386594" rpy="0 0 0" />
      <mass value="0.0703261410665101" />
      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
    </inertial>
    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
  </link>
  <joint name="L6" type="continuous">
    <origin xyz="0 0 0" rpy="1.5708 0 0" />
    <parent link="L5" />
    <child link="L6" />
    <axis xyz="0 0 -1" />
    <limit lower="-3.1" upper="3.1" effort="300" velocity="3" />
  </joint>

  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

</robot>

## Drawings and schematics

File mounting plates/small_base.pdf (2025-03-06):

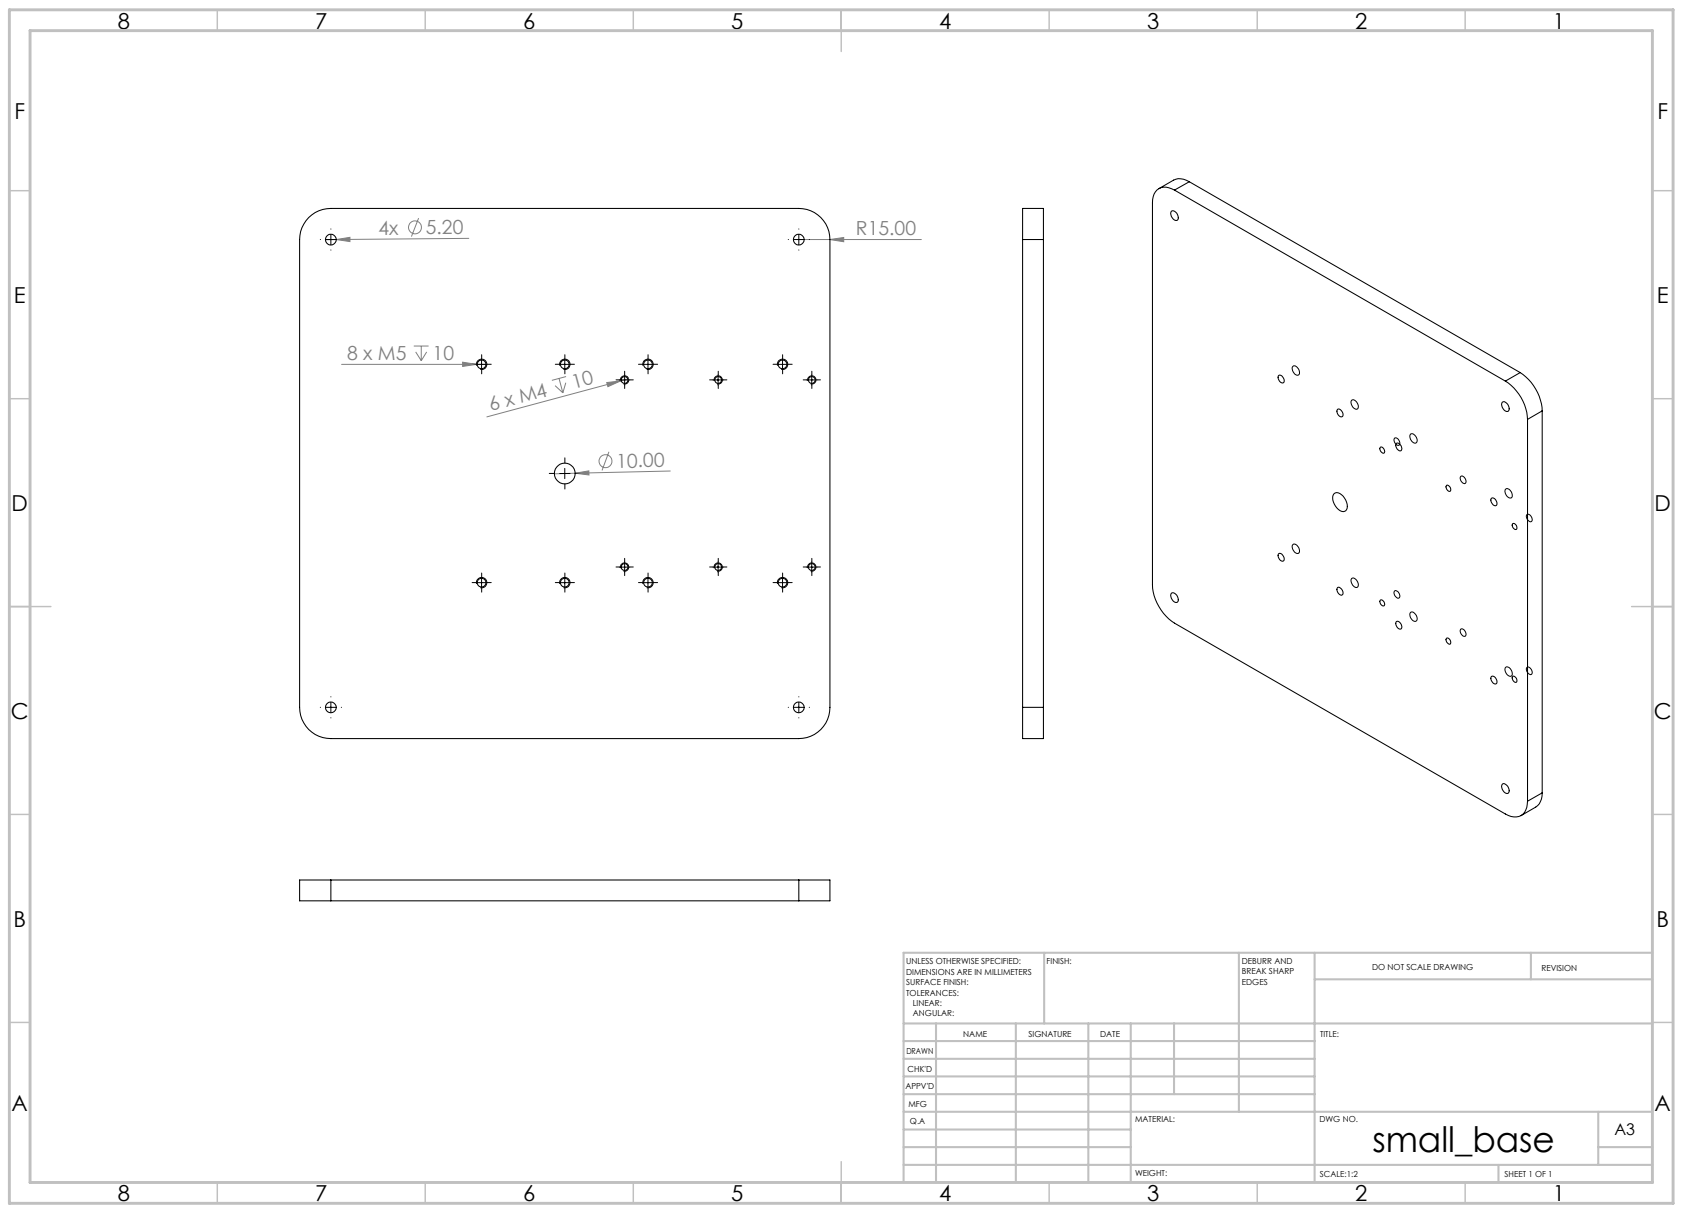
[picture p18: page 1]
FINISH:; DEBURR AND; BREAK SHARP; DO NOT SCALE DRAWING; REVISION; SCALE:1:2; SHEET 1 OF 1

UNLESS OTHERWISE SPECIFIED:
DIMENSIONS ARE IN MILLIMETERS
SURFACE FINISH:
TOLERANCES:
LINEAR:
ANGULAR:

NAME | SIGNATURE | DATE | | | | TITLE:

DRAWN
CHK'D
APPV'D
MFG
Q.A | | | | MATERIAL: | DWG NO. small_base | A3

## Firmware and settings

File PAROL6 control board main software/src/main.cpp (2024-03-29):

/** @file main.cpp
    @brief A Documented file.

    Main file of PAROL6 mainboard firmware.
    Author: Petar Crnjak
    license:
    Date:
    GUI compatible version:
    Robot compatible version:

*/

#include <TMCStepper.h>
#include <Arduino.h>
#include <AccelStepper.h>
#include <Arduino.h>
#include "hw_init.h"
#include "iodefs.h"
#include "utils.h"
#include "common.h"
#include "constants.h"
#include "adc_init.h"
#include "stm32f4xx_hal.h"
#include "motor_init.h"
#include "CAN.h"
#include "coms_CAN.h"

// HardwareSerial Serial2(USART2); // compiles
#define Serial SerialUSB
#define DEBUG 0      // For stepper drivers debug
#define DEBUG_COMS 0 // comms debug

volatile unsigned tick_count;

#define NUM 6

// Init structures
TMC5160Stepper driver[] = {TMC5160Stepper(SELECT1, R_SENSE), TMC5160Stepper(SELECT6, R_SENSE), TMC5160Stepper(SELECT5, R_SENSE),
                           TMC5160Stepper(SELECT4, R_SENSE), TMC5160Stepper(SELECT2, R_SENSE), TMC5160Stepper(SELECT3, R_SENSE)};

AccelStepper stepper[] = {AccelStepper(stepper[0].DRIVER, PUL1, DIR1), AccelStepper(stepper[5].DRIVER, PUL6, DIR6),
                          AccelStepper(stepper[4].DRIVER, PUL5, DIR5), AccelStepper(stepper[3].DRIVER, PUL4, DIR4), AccelStepper(stepper[1].DRIVER, PUL2, DIR2), AccelStepper(stepper[2].DRIVER, PUL3, DIR3)};

struct MotorStruct Joint[NUMBER_OF_JOINTS];
struct Robot PAROL6;
// struct Gripper Comp_gripper;

// variable for mesuring elapsed time between 2 received commands
int current_tick = 0;
int prev_tick = 0;

// variables for robot homing
int robot_homed = 0;
int homed = 0;
int repet_flag = 0;
int home_command = 0;

void Init_motor_drivers(int num);
int home_all();
void Init_motor_direction();
void disable_motors();
void enable_motors();

// Input helper variables
byte input_byte = 0; // Here save incoming bytes from serial

byte start_cond1_byte = 255;
byte start_cond2_byte = 255;
byte start_cond3_byte = 255;

byte end_cond1_byte = 1;
byte end_cond2_byte = 2;

byte start_cond1 = 0; // Flag if start_cond1_byte is received
byte start_cond2 = 0; // Flag if start_cond2_byte is received
byte start_cond3 = 0; // Flag if start_cond3_byte is received

byte good_start = 0; // Flag if we got all 3 start condition bytes
byte data_len = 0;   // Length of the data after -3 start condition bytes and length byte, so -4 bytes

byte data_buffer[255]; // Here save all data after data length byte
byte data_counter = 0; // Data counter for incoming bytes; compared to data length to see if we have correct length

// 255 255 255 5 2 3 3 0 1
/// @brief Data for output stuff
uint8_t start_bytes[] = {0xff, 0xff, 0xff};
uint8_t data_led = 0x05;
// uint8_t test_data[] = {0x02, 0x03, 0x03};
uint8_t test_data[] = {2, 3, 3};
uint8_t end_bytes[] = {0x01, 0x02};

TIM_TypeDef *Instance = TIM2;
HardwareTimer *MyTim = new HardwareTimer(Instance);

// FOR PNEUMATIC GRIPPER 8900
int j5_homing_offset = 8900; // for SSG48 GRIPPER 8035;

// Home commands
int run_once = 0;
int joint123_stage1 = 0;
int joint123_stage2 = 0;
int joint123_stage3 = 0;
int joint123_done = 0;

int J4_stage2 = 0;
int J4_stage3 = 0;
int J4_stage4 = 0;
int J4_done = 0;

int J6_stage2 = 0;
int J6_stage3 = 0;
int J6_stage4 = 0;
int J6_done = 0;

int J5_stage2 = 0;
int J5_stage3 = 0;
int J5_stage4 = 0;
int J5_done = 0;

int joint456_stage1 = 0;
int joint456_stage2 = 0;
int joint456_stage3 = 0;

/// demo stage test
int setup_var = 0;
int move1 = 0;
int move2 = 0;
int move3 = 0;
int move4 = 0;
int start_stop = 0;

/// @brief Called when timer for mesuring time between commands overflows, does nothing
/// @param
void Update_IT_callback(void)
{
}

void Unpack_data(uint8_t *data_buffer);
void Pack_data();
void Pack_data_TEST();
void Get_data();
void reset_homing();
void Handle_gripper();

void setup()
{

  /// Init Joint sturctures
  Init_Joint_1(&Joint[0]);
  Init_Joint_2(&Joint[1]);
  Init_Joint_3(&Joint[2]);
  Init_Joint_4(&Joint[3]);
  Init_Joint_5(&Joint[4]);
  Init_Joint_6(&Joint[5]);

  /// Init motor directions
  Init_motor_direction();
  /// Init Inputs
  Init_Digital_Inputs();
  /// Init Outputs
  Init_Digital_Outputs();

  // enable supply pin
  digitalWrite(SUPPLY_ON_OFF, HIGH);

  // Disable all stepper drivers with hardware enable pin
  digitalWrite(GLOBAL_ENABLE, HIGH);
// Delay so you can catch serial
#if (DEBUG > 0)
  delay(3000);
#endif

  // SPI1, and SPI4 can communicate at up to 45 Mbits/s, SPI2 and
  // SPI3 can communicate at up to 22.5 Mbit/s.
  // Init SPI (SPI 1 is used)
  SPI.setMOSI(MOSI);
  SPI.setMISO(MISO);
  SPI.setSCLK(SCK);
  SPI.setClockDivider(SPI_CLOCK_DIV4); // High speed (180 / 4 = 45 MHz SPI_1 speed)
  SPI.begin();
  // NOTE this delay is needed for normal operation of Power_switch_managment
  delay(200);

  /// Init ADC
  HAL_Init();
  MX_ADC1_Init();
  HAL_ADC_MspInit_(&hadc1);

  // Enable all stepper drivers with hardware enable pin
  digitalWrite(GLOBAL_ENABLE, LOW);
  // Sets some initial parameters to stepper drivers

  for (int i = 0; i < 6; i++)
  {
    Init_motor_drivers(i);
    delay(90);
  }

  stepper[5].setMaxSpeed(50000);
  stepper[5].setAcceleration(100);
  stepper[5].setSpeed(0);

  stepper[0].setMaxSpeed(50000);
  stepper[0].setAcceleration(1000);
  stepper[0].setSpeed(0);

  stepper[1].setMaxSpeed(50000);
  stepper[1].setAcceleration(1000);
  stepper[1].setSpeed(0);

  stepper[2].setMaxSpeed(50000);
  stepper[2].setAcceleration(500);
  stepper[2].setSpeed(0);

  stepper[3].setMaxSpeed(50000);
  stepper[3].setAcceleration(500);
  stepper[3].setSpeed(0);

  stepper[4].setMaxSpeed(50000);
  stepper[4].setAcceleration(500);
  stepper[4].setSpeed(0);

  /// Freq is 90Mhz, with 128 prescale we get 703125, timer is 16bit
  /// It counts to 65535. 1 Tick is then equal to 1/703125 = 1.422222e-6
  /// To get 10 ms we need 7031 ticks
  MyTim->setPrescaleFactor(128);
  MyTim->attachInterrupt(Update_IT_callback);
  MyTim->resume();
  Serial.begin(3000000);
  Setup_CAN_bus();
}

void loop()
{

  /*
  int state1 = digitalRead(INPUT1);
  int state2 = digitalRead(INPUT2);
  Serial.println("inputs 1 is:");
  Serial.println(state1);
  Serial.println("inputs 2 is:");
  Serial.println(state2);
  delay(2000);
  */

  Power_switch_managment();
  static uint32_t last_time = 0;
  int ms = HAL_GetTick();

  if ((ms - last_time) > 3000) // run every 3s
  {
    last_time = ms;
  }

  /// Robot repetability

  if (PAROL6.command == 69)
  {
    if (setup_var == 0)
    {
      setup_var = 1;

      stepper[0].setMaxSpeed(6000);
      stepper[0].setAcceleration(6000);
      stepper[0].moveTo(6179);

      stepper[1].setMaxSpeed(4000);
      stepper[1].setAcceleration(4000);
      stepper[1].moveTo(-22222);

      stepper[2].setMaxSpeed(3500);
      stepper[2].setAcceleration(3500);
      stepper[2].moveTo(49812);

      stepper[3].setMaxSpeed(3500);
      stepper[3].setAcceleration(3500);
      stepper[3].moveTo(0);

      stepper[4].setMaxSpeed(3500);
      stepper[4].setAcceleration(3500);
      stepper[4].moveTo(4059);

      stepper[5].setMaxSpeed(7500);
      stepper[5].setAcceleration(7500);
      stepper[5].moveTo(46075);

      /// init accels
      move1 = 1;
    }

    if (move1 == 1)
    {

      for (int i = 0; i < 6; i++)
      {
        stepper[i].run();
      }

      if (stepper[0].isRunning() || stepper[1].isRunning() || stepper[2].isRunning() || stepper[3].isRunning() || stepper[4].isRunning() || stepper[5].isRunning())
      {
        move1 = 1;
      }
      else
      {
        move1 = 0;
        move2 = 1;
        stepper[0].moveTo(10240);
        stepper[1].moveTo(-32000);
        stepper[2].moveTo(57905);
        stepper[3].moveTo(0);
        stepper[4].moveTo(0);
        stepper[5].moveTo(32000);
        delay(2000);
      }
    }

    if (move2 == 1)
    {

      for (int i = 0; i < 6; i++)
      {
        stepper[i].run();
      }

      if (stepper[0].isRunning() || stepper[1].isRunning() || stepper[2].isRunning() || stepper[3].isRunning() || stepper[4].isRunning() || stepper[5].isRunning())
      {
        move2 = 1;
      }
      else
      {
        move2 = 0;
        setup_var = 1;
      }
    }
  }

  // Dummy command
  if (PAROL6.command == 255)
  {
    setup_var = 0;
    move1 = 0;
    move2 = 0;
    if (home_command == 0)
    {
      for (int i = 0; i < 6; i++)
      {
        stepper[i].setSpeed(Joint[i].commanded_velocity);
        //  provjera da li smo na većim pozicijama, ako da baci error
      }
    }
  }

  /// Enable robot
  if (PAROL6.command == 101)
  {
    reset_homing();
    home_command = 0;
    PAROL6.disabled = 0;
  }

  /// Disable robot
  if (PAROL6.command == 102)
  {
    home_command = 0;
    PAROL6.disabled = 1;
  }

  /// Clear error
  if (PAROL6.command == 103)
  {
    home_command = 0;
    reset_homing();
  }

  // If robot is disabled, disable all move commands
  if (PAROL6.disabled == 0)
  {
    /// Home robot
    if (PAROL6.command == 100)
    {
      home_command = 1;
      homed = 0;
      if (homed == 0)
      {
        home_all();
      }
      else
      {
        home_command = 0;
      }
    }
    else if (PAROL6.command == 255 && home_command == 1)
    {
      if (homed == 0)
      {
        home_all();
      }
      else
      {
        home_command = 0;
      }
    }

    /// JOG
    if (PAROL6.command == 123)
    {
      home_command = 0;
      homed = 1;
      for (int i = 0; i < 6; i++)
      {
        stepper[i].setSpeed(Joint[i].commanded_velocity);
        stepper[i].runSpeed();
      }
      // Joint[i].speed = Joint[i].commanded_velocity;
      //  provjera da li smo na većim pozicijama, ako da baci error

      /// Pročitaj koji je od joint speeds nije nula i miči taj joint tom brzinom
      // If (current position != commanded) // ovo vrijedi za one position command tip naredbe
      // Set speed
      // Run speed
      // Dummy data sets sppeds to zero
    }

    /// GO 2 POSITION
    /// Input is needed position and speed
    if (PAROL6.command == 156)
    {
      home_command = 0;
      homed = 1;

      for (int i = 0; i < 6; i++)
      {

        int speed_set = int(((Joint[i].commanded_position - Joint[i].position) / 0.01));
        speed_set = int(((Joint[i].commanded_velocity + speed_set) / 2));
        stepper[i].setSpeed(speed_set);
        stepper[i].runSpeed();
      }
    }
  }

  /***************************************************/
  /***************************************************/
  /// Here check robot position and speed and save to struct
  for (int i = 0; i < 6; i++)
  {
    Joint[i].position = stepper[i].currentPosition();
    Joint[i].speed = stepper[i].speed();
    // provjera da li smo na većim pozicijama, ako da baci error
  }
  /***************************************************/
  /***************************************************/

  Get_data();
}

/// @brief  Here we receive data from the PC and unpack it.
/// If the data is good we also send a packet to the PC
void Get_data()
{

  // Get data from CAN gripper
  CAN_protocol(Serial);

  // Get data from serial
  while (Serial.available() > 0)
  {

    input_byte = Serial.read();
    //  When data len is received start is good and after that put all data in receive buffer
    //  Data len is ALL data after it; that includes input buffer, end bytes and CRC
    if (good_start != 1)
    {
      // All start bytes are good and next byte is data len
      if (start_cond1 == 1 && start_cond2 == 1 && start_cond3 == 1)
      {
        good_start = 1;
        data_len = input_byte;
        // Serial.println("Robot good start");
      }
      // Third start byte is good
      if (input_byte == start_cond3_byte && start_cond2 == 1 && start_cond1 == 1)
      {
        start_cond3 = 1;
        // Serial.println("Robot good cond 3");
      }
      // Third start byte is bad, reset all flags
      else if (start_cond2 == 1 && start_cond1 == 1)
      {
        start_cond1 = 0;
        start_cond2 = 0;
      }
      // Second start byte is good
      if (input_byte == start_cond2_byte && start_cond1 == 1)
      {
        start_cond2 = 1;
        // Serial.println("Robot good cond 2");
      }
      // Second start byte is bad, reset all flags
      else if (start_cond1 == 1)
      {
        start_cond1 = 0;
      }
      // First start byte is good
      if (input_byte == start_cond1_byte)
      {
        start_cond1 = 1;
        // Serial.println("Robot good cond 1");
      }
    }
    else
    {
      // Here data goes after good start
      data_buffer[data_counter] = input_byte;
      if (data_counter == data_len - 1)
      {
        // Here if last 2 bytes are end condition bytes we process the data
        if (data_buffer[data_len - 2] == end_cond1_byte && data_buffer[data_len - 1] == end_cond2_byte)
        {

          // Serial.println(data_buffer[data_len-2]); // 1
          // Serial.println(data_buffer[data_len-1]); // 1
          //  Serial.println(data_buffer[data_len]); // 0
          // Serial.println("ROBOT GOOD END CONDITION ");
          current_tick = MyTim->getCount();
          PAROL6.time_between_commands = current_tick - prev_tick;
          prev_tick = current_tick;
          // Serial.println("ROBOT DATA UNPACK ");
          Unpack_data(data_buffer);
          // Serial.println("ROBOT DATA PACK");

          // Read estop and inputs and write outputs
          
          PAROL6.In1 = digitalRead(INPUT1);
          PAROL6.In2 = digitalRead(INPUT2);
          PAROL6.Estop = digitalRead(ESTOP);
          digitalWrite(OUTPUT1, PAROL6.commanded_OUT1);
          digitalWrite(OUTPUT2, PAROL6.commanded_OUT2);
          PAROL6.Out1 = PAROL6.commanded_OUT1;
          PAROL6.Out2 = PAROL6.commanded_OUT2;

          Handle_gripper();
          Pack_data();
          // digitalWrite(DIR6,HIGH);
          // digitalWrite(DIR6,LOW);
          //   ako su dobri izračunaj crc
          //   if crc dobar raspakiraj podatke
          //   ako je dobar paket je dobar i spremi ga u nove variable!
          //  Pošalji nove podatke od robota
        }

        // Serial.println("podaci u data bufferu su: ");
        // for (int i = 0; i < data_len; i++)
        // Serial.println(data_buffer[i]);

        good_start = 0;
        start_cond1 = 0;
        start_cond3 = 0;
        start_cond2 = 0;
        data_len = 0;
        data_counter = 0;
      }
      else
      {
        data_counter = data_counter + 1;
      }
    }
  }
}

void Handle_gripper()
{

  
    /// Here unpack gripper command data to bits and see what needs to be sent to the gripper
    bool bitArray[8]; // 0 - activation, 1 - action status, 2 - estop status, 3 - release dir
  // Comp_gripper.mode; 1 - calibration, 0 - operation mode

  byteToBitsBigEndian(Comp_gripper.command, bitArray);

  if (Comp_gripper.mode == 1)
  {
    Send_gripper_cal();
  }
  else if (Comp_gripper.mode == 2)
  {
    Send_clear_error();
  }
  else if (Comp_gripper.prev_commanded_position == Comp_gripper.commanded_position && Comp_gripper.prev_commanded_speed == Comp_gripper.commanded_speed 
  && Comp_gripper.prev_commanded_current == Comp_gripper.commanded_current && Comp_gripper.prev_command == Comp_gripper.command && Comp_gripper.prev_commanded_ID == Comp_gripper.commanded_ID
  && Comp_gripper.mode == 0)
  {
    Send_gripper_pack_empty();
  }
  else
  {
    Send_gripper_pack();
  }

  Comp_gripper.prev_commanded_position = Comp_gripper.commanded_position;
  Comp_gripper.prev_commanded_speed = Comp_gripper.commanded_speed;
  Comp_gripper.prev_commanded_current = Comp_gripper.commanded_current;
  Comp_gripper.prev_command = Comp_gripper.command;
  Comp_gripper.prev_commanded_ID = Comp_gripper.commanded_ID;
}

/// @brief  Unpack data packet we got from the PC
/// @param data_buffer array of bytes we get thru serial
void Unpack_data(uint8_t *data_buffer)
{

  int temp[6][3];
  int Joints[6];
  int Speed[6];
  int Command;
  int Affected_joint;
  int InOut;
  int Timeout;
  int Gripper_position;
  int Gripper_speed;
  int Gripper_current;
  int Gripper_command;
  int Gripper_mode;
  int Gripper_ID;
  int CRC_byte;

  int i, j;
  /// Unpack position data
  for (i = 0, j = 0; i < 18; i += 3, j++)
  {
    temp[j][0] = data_buffer[i];
    temp[j][1] = data_buffer[i + 1];
    temp[j][2] = data_buffer[i + 2];
    uint8_t buf_test[] = {temp[j][0], temp[j][1], temp[j][2]};
    Joints[j] = bytes_to_int(buf_test);
    Joint[j].commanded_position = Joints[j];

    // Serial.println(Joints[j]);
  }
  /// Unpack speed data
  for (i = 18, j = 0; i < 36; i += 3, j++)
  {
    temp[j][0] = data_buffer[i];
    temp[j][1] = data_buffer[i + 1];
    temp[j][2] = data_buffer[i + 2];
    uint8_t buf_test[] = {temp[j][0], temp[j][1], temp[j][2]};
    Speed[j] = bytes_to_int(buf_test);
    Joint[j].commanded_velocity = Speed[j];
    // Serial.println(Speed[j]);
  }

  Command = data_buffer[36];
  PAROL6.command = Command;
  // Serial.println(Command);
  Affected_joint = data_buffer[37];
  PAROL6.Affected_joint = Affected_joint;
  // Serial.println(Affected_joint);
  InOut = data_buffer[38];
  bool bitArray[8];
  byteToBitsBigEndian(InOut, bitArray);
  PAROL6.commanded_OUT1 = bitArray[2];
  PAROL6.commanded_OUT2 = bitArray[3];
  // Serial.println(InOut);
  Timeout = data_buffer[39];
  PAROL6.Timeout = Timeout;
  // Serial.println(Timeout);

  uint8_t buf_test[2] = {data_buffer[40], data_buffer[41]};
  Gripper_position = two_bytes_to_int(buf_test);
  Comp_gripper.commanded_position = Gripper_position;
  // Serial.println(Gripper_position);

  buf_test[0] = data_buffer[42];
  buf_test[1] = data_buffer[43];
  Gripper_speed = two_bytes_to_int(buf_test);
  Comp_gripper.commanded_speed = Gripper_speed;
  // Serial.println(Gripper_speed);

  buf_test[0] = data_buffer[44];
  buf_test[1] = data_buffer[45];
  Gripper_current = two_bytes_to_int(buf_test);
  Comp_gripper.commanded_current = Gripper_current;
  // Serial.println(Gripper_current);

  Gripper_command = data_buffer[46];
  Comp_gripper.command = Gripper_command;
  // Serial.println(Gripper_command);
  Gripper_mode = data_buffer[47];
  Comp_gripper.mode = Gripper_mode;
  // Serial.println(Gripper_mode);
  Gripper_ID = data_buffer[48];
  Comp_gripper.commanded_ID = Gripper_ID;
  // Serial.println(Gripper_ID);
  CRC_byte = data_buffer[49];
  // Serial.println(CRC_byte);

#if (DEBUG_COMS > 0)
  for (i = 0, j = 0; i < 18; i += 3, j++)
  {
    Serial.println(Joints[j]);
  }
  for (i = 0, j = 0; i < 18; i += 3, j++)
  {
    Serial.println(Speed[j]);
  }
  Serial.println(Command);
  Serial.println(Affected_joint);
  Serial.println(InOut);
  Serial.println(Timeout);
  Serial.println(Gripper_position);
  Serial.println(Gripper_speed);
  Serial.println(Gripper_current);
  Serial.println(Gripper_command);
  Serial.println(Gripper_mode);
  Serial.println(Gripper_ID);
  Serial.println(CRC_byte);

#endif
}

/// @brief  Pack data packet that we will send to the PC
/// Test function
void Pack_data_TEST()
{

  // Len is defined by all bytes EXCEPT start bytes and len
  uint8_t start_bytes[] = {0xff, 0xff, 0xff}; // 3
  int len = 56;
  int Position_out[] = {255, 254, 253, 252, 251, 250}; // 18
  int Speed_out[] = {245, 244, 243, 242, 241, 240};    // 18
  bool Homed[] = {1, 1, 1, 1, 1, 1, 1, 1};             // 1
  bool IO_var[] = {0, 0, 0, 0, 0, 0, 0, 0};            // 1
  bool temp_error[] = {1, 1, 1, 1, 1, 1, 1, 1};        // 1
  bool position_error[] = {0, 0, 0, 0, 0, 0, 0, 0};    // 1
  int timing_data = 255;                               // 2 byte
  int timeout_error = 244;                             // 1
  int xtr2 = 255;                                      // 1
  int gripper_ID = 200;                                // 1
  int gripper_position = 300;                          // 2 byte
  int gripper_speed = 300;                             // 2 byte
  int gripper_current = 300;                           // 2 byte
  int gripper_status = 200;                            // 1
  int object_detection = 1;                            // 1
  int CRC_byte = 212;                                  // 1
  uint8_t end_bytes[] = {0x01, 0x02};                  // 2

  byte data_buffer_send[3];

  // Send start bytes
  Serial.write(start_bytes[0]);
  Serial.write(start_bytes[1]);
  Serial.write(start_bytes[2]);

  Serial.write(len);

  /// Position data
  for (int i = 0; i < 6; i++)
  {
    intTo3Bytes(Position_out[i], data_buffer_send);
    Serial.write(data_buffer_send[0]);
    Serial.write(data_buffer_send[1]);
    Serial.write(data_buffer_send[2]);
  }
  /// Speed data
  for (int i = 0; i < 6; i++)
  {
    intTo3Bytes(Speed_out[i], data_buffer_send);
    Serial.write(data_buffer_send[0]);
    Serial.write(data_buffer_send[1]);
    Serial.write(data_buffer_send[2]);
  }
  /// Homed data
  Serial.write(bitsToByte(Homed));

  /// I/O data
  Serial.write(bitsToByte(IO_var));

  /// temperature error
  Serial.write(bitsToByte(temp_error));

  /// positon error
  Serial.write(bitsToByte(position_error));

  // Dummy timing data
  Serial.write(255);
  Serial.write(255);

  // Timeout error
  Serial.write(timeout_error);

  /// Aditional data slot
  Serial.write(xtr2);

  /// Gripper ID
  Serial.write(gripper_ID);

  // Send gripper positon
  intTo2Bytes(gripper_position, data_buffer_send);
  Serial.write(data_buffer_send[0]);
  Serial.write(data_buffer_send[1]);

  // Send gripper speed
  intTo2Bytes(gripper_speed, data_buffer_send);
  Serial.write(data_buffer_send[0]);
  Serial.write(data_buffer_send[1]);

  // Send gripper current
  intTo2Bytes(gripper_current, data_buffer_send);
  Serial.write(data_buffer_send[0]);
  Serial.write(data_buffer_send[1]);

  Serial.write(gripper_status);

  // Send gripper object detected
  Serial.write(object_detection);

  // Send CRC
  Serial.write(CRC_byte);

  // Send end bytes
  Serial.write(end_bytes[0]);
  Serial.write(end_bytes[1]);
}
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

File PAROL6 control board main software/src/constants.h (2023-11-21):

/** @file constants.h
    @brief A Documented file.
    
    Here declare all constant variables
    For schematic please refer to:
    For additional pin functionality refer to:

*/

#ifndef CONSTANTS_H
#define CONSTANTS_H

#define VERSION 1

#define ID 1

#define ADC_RESOLUTION 12

#define R_SENSE 0.075f

#define NUMBER_OF_JOINTS 6

#define MICROSTEP 32

#define MOTOR1_MAX_CURRENT 2000 // Max 2100
#define MOTOR2_MAX_CURRENT 2000 // Max 2100
#define MOTOR3_MAX_CURRENT 1900 // Max 2000
#define MOTOR4_MAX_CURRENT 1700 // Max 2000 but since the motors are enclosed reduce it
#define MOTOR5_MAX_CURRENT 1700 // Max 2000 but since the motors are enclosed reduce it
#define MOTOR6_MAX_CURRENT 965 // Max 1000

#endif

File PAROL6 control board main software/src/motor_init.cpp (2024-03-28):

/// HERE INIT STRUCTURES??
#include "motor_init.h"

void Init_motor_struct(struct MotorStruct *Joint__)
{

    Joint__->LIMIT = 200;
}

void Init_Joint_1(struct MotorStruct *Joint__)
{
    // J1 is special because we usually go to the position that 
    // is +90 deg from its Denevit Hartenberg standby positon 
    // + 90 deg is equal to 9600 steps in 32microstep range
    Joint__->standby_position = 10240; // 10240   // 9600
    Joint__->homed_position = 13500; // 13653  // 13500
    Joint__->motor_max_current = MOTOR1_MAX_CURRENT;
    Joint__->motor_max_speed = 0;
    Joint__->motor_max_acceleration = 0;
    Joint__->motor_min_speed = 0;
    Joint__->motor_min_acceleration = 0;
    Joint__->joint_range_positive = 0;
    Joint__->joint_range_negative = 0;
    Joint__->joint_range_positive_steps = 14000;
    Joint__->joint_range_negative_steps = -14000;
    Joint__->homed = 0;
    Joint__->homing = 0;
    Joint__->temperature_error = 0;
    Joint__->temperature_warrning = 0;
    Joint__->microstep = MICROSTEP;
    Joint__->limit_switch_trigger = 0; // temp since sensor is faulty?
    Joint__->reduction_ratio = 6.4; // 96 / 15
    Joint__->position = -200;
    Joint__->speed = -100;
    Joint__->current = 0;
    Joint__->LIMIT = LIMIT6;
    Joint__->DIR = DIR1;
    Joint__->STEP = PUL1;
    Joint__->SELECT = SELECT1;
    Joint__->driver_chip_on_board = 0;
    Joint__->direction_reversed = 1;
    Joint__->irun = 16;
    Joint__->ihold = 16;
    Joint__->hold_multiplier = 0.7;
    Joint__->over_temp_pre_warning = 0;
    Joint__->over_temp_warning = 0;
    Joint__->diag0 = 0;
    Joint__->open_load_B = 0;
    Joint__->open_load_A = 0;
    Joint__->short_2_gnd_B = 0;
    Joint__->short_2_gnd_A = 0;
    Joint__->position_error = 0;
}

void Init_Joint_2(struct MotorStruct *Joint__)
{
    Joint__->standby_position = -32000; 
    Joint__->homed_position = 19588;
    Joint__->motor_max_current = MOTOR2_MAX_CURRENT;
    Joint__->motor_max_speed = 0;
    Joint__->motor_max_acceleration = 0;
    Joint__->motor_min_speed = 0;
    Joint__->motor_min_acceleration = 0;
    Joint__->joint_range_positive = 0;
    Joint__->joint_range_negative = 0;
    Joint__->joint_range_positive_steps = -1200;
    Joint__->joint_range_negative_steps = -51587;
    Joint__->homed = 0;
    Joint__->homing = 0;
    Joint__->temperature_error = 0;
    Joint__->temperature_warrning = 0;
    Joint__->microstep = MICROSTEP;
    Joint__->limit_switch_trigger = 1;
    Joint__->reduction_ratio = 20;
    Joint__->position = 0;
    Joint__->speed = 0;
    Joint__->current = 0;
    Joint__->LIMIT = LIMIT2;
    Joint__->DIR = DIR6;
    Joint__->STEP = PUL6;
    Joint__->SELECT = SELECT6;
    Joint__->driver_chip_on_board = 0;
    Joint__->direction_reversed = 0;
    Joint__->irun = 16;
    Joint__->ihold = 16;
    Joint__->hold_multiplier = 0.8;
    Joint__->over_temp_pre_warning = 0;
    Joint__->over_temp_warning = 0;
    Joint__->diag0 = 0;
    Joint__->open_load_B = 0;
    Joint__->open_load_A = 0;
    Joint__->short_2_gnd_B = 0;
    Joint__->short_2_gnd_A = 0;
    Joint__->position_error = 0;
}

void Init_Joint_3(struct MotorStruct *Joint__)
{
    Joint__->standby_position = 57905;
    Joint__->homed_position = 23020;
    Joint__->motor_max_current = MOTOR3_MAX_CURRENT;
    Joint__->motor_max_speed = 0;
    Joint__->motor_max_acceleration = 0;
    Joint__->motor_min_speed = 0;
    Joint__->motor_min_acceleration = 0;
    Joint__->joint_range_positive = 0;
    Joint__->joint_range_negative = 0;
    Joint__->joint_range_positive_steps = 92605;
    Joint__->joint_range_negative_steps = 34700;
    Joint__->homed = 0;
    Joint__->homing = 0;
    Joint__->temperature_error = 0;
    Joint__->temperature_warrning = 0;
    Joint__->microstep = MICROSTEP;
    Joint__->limit_switch_trigger = 1;
    Joint__->reduction_ratio = 18.0952381; // 20 * (38 / 42)
    Joint__->position = 0;
    Joint__->speed = 0;
    Joint__->current = 0;
    Joint__->LIMIT = LIMIT3;
    Joint__->DIR = DIR5;
    Joint__->STEP = PUL5;
    Joint__->SELECT = SELECT5;
    Joint__->driver_chip_on_board = 0;
    Joint__->direction_reversed = 1;
    Joint__->irun = 16;
    Joint__->ihold = 16;
    Joint__->hold_multiplier = 0.8;
    Joint__->over_temp_pre_warning = 0;
    Joint__->over_temp_warning = 0;
    Joint__->diag0 = 0;
    Joint__->open_load_B = 0;
    Joint__->open_load_A = 0;
    Joint__->short_2_gnd_B = 0;
    Joint__->short_2_gnd_A = 0;
    Joint__->position_error = 0;
}

void Init_Joint_4(struct MotorStruct *Joint__)
{

    Joint__->standby_position = 0;
    Joint__->homed_position = -10200;
    Joint__->motor_max_current = MOTOR4_MAX_CURRENT;
    Joint__->motor_max_speed = 0;
    Joint__->motor_max_acceleration = 0;
    Joint__->motor_min_speed = 0;
    Joint__->motor_min_acceleration = 0;
    Joint__->joint_range_positive = 0;
    Joint__->joint_range_negative = 0;
    Joint__->joint_range_positive_steps = 7500;
    Joint__->joint_range_negative_steps = -7500;
    Joint__->homed = 0;
    Joint__->homing = 0;
    Joint__->temperature_error = 0;
    Joint__->temperature_warrning = 0;
    Joint__->microstep = MICROSTEP;
    Joint__->limit_switch_trigger = 0;
    Joint__->reduction_ratio = 4;
    Joint__->position = 0;
    Joint__->speed = 0;
    Joint__->current = 0;
    Joint__->LIMIT = LIMIT4;
    Joint__->DIR = DIR4;
    Joint__->STEP = PUL4;
    Joint__->SELECT = SELECT4;
    Joint__->driver_chip_on_board = 0;
    Joint__->direction_reversed = 0;
    Joint__->irun = 16;
    Joint__->ihold = 16;
    Joint__->hold_multiplier = 0.8;
    Joint__->over_temp_pre_warning = 0;
    Joint__->over_temp_warning = 0;
    Joint__->diag0 = 0;
    Joint__->open_load_B = 0;
    Joint__->open_load_A = 0;
    Joint__->short_2_gnd_B = 0;
    Joint__->short_2_gnd_A = 0;
    Joint__->position_error = 0;
}
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

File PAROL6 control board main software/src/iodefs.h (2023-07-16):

#ifndef IODEFS_H
#define IODEFS_H

#include <Arduino.h>
#include <stdio.h>

#define PUL1 PC6 
#define PUL2 PA10 
#define PUL3 PC0 
#define PUL4 PC3 
#define PUL5 PC9 
#define PUL6 PC5 

#define DIR1 PB15 
#define DIR2 PA1 
#define DIR3 PC1 
#define DIR4 PA0 
#define DIR5 PA8 
#define DIR6 PB1 

#define LIMIT1 PC12 
#define LIMIT2 PB3 
#define LIMIT3 PA15 
#define LIMIT4 PD2 
#define LIMIT5 PB4 
#define LIMIT6 PC11 

#define SELECT1 PC7 
#define SELECT2 PA9
#define SELECT3 PC15
#define SELECT4 PC2
#define SELECT5 PC8
#define SELECT6 PC4

#define GLOBAL_ENABLE PA3

#define MISO PA6
#define MOSI PA7
#define SCK PA5
#define FLASH_SELECT PA4

#define LED1 PB2
#define LED2 PB10

#define SUPPLY_ON_OFF PC10
#define SUPPLY_BUTTON_STATE PC14

#define INPUT1 PB6
#define INPUT2 PB5

#define OUTPUT1 PC13
#define OUTPUT2 PB7

#define ESTOP PB14

#define VBUS PB0  // ADC1 CHANNEL 8

#define USB_D_PLUS  PA12 
#define USB_D_MINUS PA11 

#define CAN1TX PB9
#define CAN1RX PB8

#define CAN1TX PB13
#define CAN1RX PB12


#endif

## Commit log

2023-09-06 changed bom
2023-10-17 added testing code
    [PAR6_mainboard_v1.csv, bom.csv, designators.csv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]
2023-10-29 added urdf
    [L1.STL, L2.STL, L3.STL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]
2023-10-30 update on bom and instructions
2023-10-31 small change
    [J1_belt_cover_rework.STL]
2023-11-02 Updated BOM
2023-11-09 added excel bom
    [PAROL_BOM_excel.xlsx]
2023-11-11 updated print table
    [PR_EXCEL.xlsx]
2023-11-14 small bom update
    [PAROL_BOM_9_11_2023.xlsx, PAROL_BOM_excel.xlsx]
2023-11-16 UPDATE BOM
    [PAROL_BOM_9_11_2023.xlsx]
2023-11-18 BOM change
    [PAROL_BOM_18_11_2023.xlsx, PAROL_BOM_9_11_2023.xlsx]
2023-11-21 Update constants.h
    update currents
2023-12-11 Updated fan cover
2024-01-04 stl folder change
    [J1_wires_cover_rework.STL]
2024-01-10 update on BOM
    add estop assembly instruction, updated bom with stlink and parts for estop
    [PAROL_BOM_12_12_2023.xlsx, PAROL_BOM_1_1_2024.xlsx]
2024-02-09 Update on BOM
    [PAROL BOM.xlsx, PAROL_BOM_1_1_2024.xlsx]
2024-03-02 added support for CAN bus
2024-03-02 Added support for CAN1 and compliant gripper
2024-03-28 Update to building instructions
    Added gripper
2024-03-28 update for using the gripper
2024-03-29 updates to BOM and assembly manual
    [PAROL BOM.xlsx]
2024-05-12 added powerpoint version
2025-01-29 update BOM with alternatives
    [PAROL BOM.xlsx]
2025-02-02 Added drivers for stlink
2025-03-04 BOM update
    [PAROL6 BOM.xlsx]
2025-03-06 Added mounting plates
    [big_base.STEP, small_base.STEP]
2025-04-30 updated URDF with joint limits
    [PAROL6.urdf, joint_trajectroy_controller.yaml]
2025-09-23 Updated BOM added CAN test python file
    [PAROL6 BOM OLD.xlsx]
2025-09-23 Added updated BOM
2025-11-13 added horizontal gripper
    [Pneumatic_gripper_holder_custom.stl, Pneumatic_gripper_holder_horizontal.stl]
2025-12-12 Upadte BOM links

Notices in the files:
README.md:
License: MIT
